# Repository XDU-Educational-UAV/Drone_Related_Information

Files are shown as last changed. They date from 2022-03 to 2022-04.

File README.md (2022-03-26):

微型四轴飞行器外形:

         HEAD
	M4  ↑  M1
	   \     /
	    \   /
	     \ /
	     / \
	    /   \
	   /     \
	M3     M2
	
硬件资源:

1. MCU:STM32G030K8T6 (FLASH:512K, RAM:128K, 系统运行时钟频率:96MHz)
2. 6轴MPU6050连接在IIC1上(IMU_SCL:PB8, IMU_SDA:PB7, 通信方式:模拟IIC)
3. 蓝牙无线通信NFR51822连接在UART1上(RXD:PA3, TXD:PA2, NRF_FLOW_CTRL:PA4)
4. MOTOR1连接在TIM4_CH2上(PB6)
5. MOTOR2连接在TIM4_CH1上(PB3)
6. MOTOR3连接在TIM2_CH3上(PA9/PA11)
7. MOTOR4连接在TIM2_CH1上(PB8)
8. MOTOR1对应的绿色LED，连接在PB5上，高电平有效
9. MOTOR2对应的绿色LED，连接在PB4上，高电平有效
10. MOTOR3对应的绿色LED，连接在PC8上，高电平有效
11. MOTOR4对应的绿色LED，连接在PB9上，高电平有效

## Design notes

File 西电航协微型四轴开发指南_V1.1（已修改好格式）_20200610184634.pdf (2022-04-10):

XDU Aero Association | 西电航协

51 /
58

# 西电航协微型四轴开发指南

主编&项目策划： | 西安电子科技大学 电子工程学院 吕瑞涛
硬件设计： | 西安电子科技大学 电子工程学院 王晗宇
机械设计： | 西安电子科技大学 空间科学与技术学院 程天宇
软件设计： | 西安电子科技大学 电子工程学院 吕瑞涛 李妍榕

### User Manual

用户手册

目 录

目录

# 1. 四轴飞行器的基本组成

四轴飞行器主要是由电机、电调、电池、浆叶、机架、遥控器、飞控组成。下面我们 分别以我们微型四轴及市场上常见的 DIY 大四轴来介绍这些部件。

# 1.1 电机

电机分为有刷电机和无刷电机两类，分别如图 1.1.1 和图 1.1.2 所示。

图 1.1.1 空心杯电机 | 图 1.1.2 无刷电机

有刷电机体积小价格便宜而且控制简单，比较适用于做微型四轴。我们设计的微型四 轴就是采用了图 1.1.1 空心杯有刷电机，型号为 716。 无刷电机体积稍大，载重能力强，比较适用于 DIY 大四轴。无刷电机控制需要搭配专 门的无刷电机电调模块。如图 1.1.2 无刷电机，2212 1200KV，22 表示电机的外转子直径为 22mm；12 表示转子的高度为 12mm；1200KV 表示电压每增加 1V 电机的转速增加

## 1200r/min。

# 1.2 MOS 管和电调

微型四轴和大四轴一般分别使用 MOS 管和电调驱动电机，MOS 管和电调分别如图

## 1.2.1 和 1.2.2 所示：

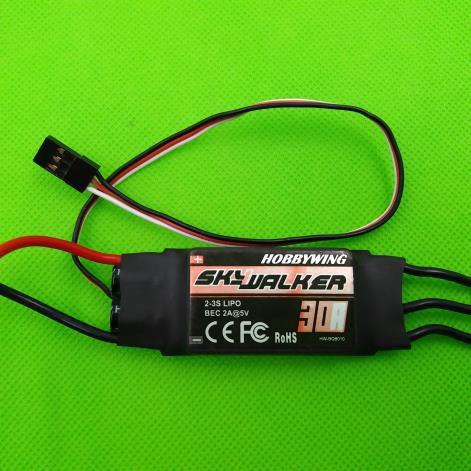
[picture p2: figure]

图 1.2.1 MOS 管 | 图 1.2.2 无刷电机电调模块

电调即为电子调速器，控制电机转动、停止及转速。
有刷电机电调通常只需要一个 MOS 管，飞控输出 PWM 即可控制电机。我们设计的 微型四轴采用如图 1.2.1 所示 SOT-23 封装的 MOS 管，型号为：SI2302。

无刷电机电调模块如图 1.2.2 所示。无刷电机电调模块内部通常由一个 MCU 和三相 桥电路组成，MCU 通过控制三相桥来实现无刷电机换相。同样，无刷电机电调模块也只需 飞控输出 PWM 即可控制电机。

## 1.3 航模电池

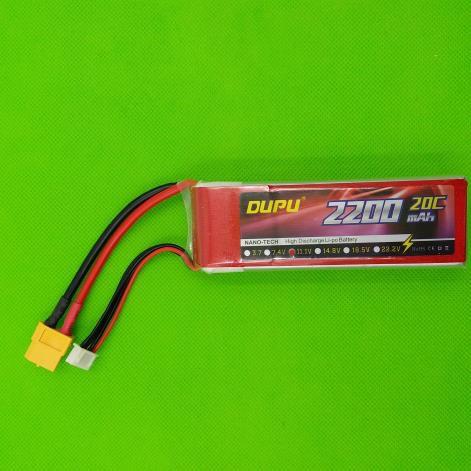
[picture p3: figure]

微型四轴选用的锂电池如图 1.3.1 所示，参数为 250mAh 20C 1S。DIY 大四轴常用的 锂电池如 1.3.2 所示。

图 1.3.1 250mAh 20C 1S 锂电池 | 图 1.3.2 2200mAh 20C 3S 锂电池
下面我们对这些参数做一下解释。
电池容量 mAh：锂电池的容量，如 2000mAh 的电池，以 2000mA 放电，可持续放电 1 小时；以 1000mA 放电，可持续放电 2 小时。
电池节数：电池 2S、3S、4S 代表锂电池节数。锂电池 1 节的标准电压为 3.7V，3S 代表有 3 节 3.7V 的电池在里面，电压为 11.1V。
电池放电倍率 C：四轴一般使用的动力锂电池，也是放电倍率 C 较大。普通锂电池放 电倍率通常为 1C 或者 0.5C，动力电池则为十几二十 C。如标称 250mAh 20C 的电池，它 的放电电流为 250ma×20，即为 5A 放电电流。

# 1.4 正反桨

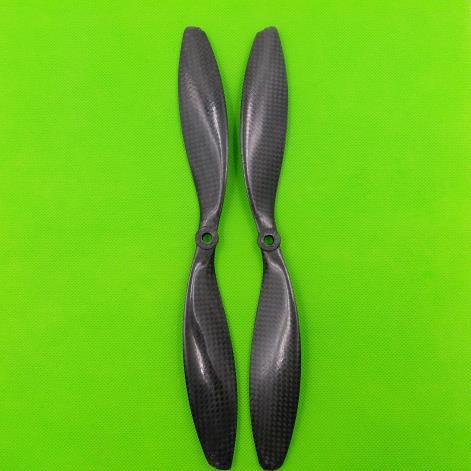
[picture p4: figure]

微型四轴选用如图 1.4.1 所示，直径为 46mm 的浆叶，带 A 字的浆为正浆。图 1.4.2 1038 正反浆叶为 DIY 大四轴所用的浆叶，1038 表示直径 10 英寸，螺距 3.8 英寸。

图 1.4.1 46mm 正反浆叶 | 图 1.4.2 1038 正反浆叶

四轴飞行器为什么需要正反浆叶？
答：浆叶旋转时会产生自旋力导致四轴自旋，为了抵消自旋力相隔电机的浆叶旋转方向要 不一样，但是浆的风都是要往下吹，这就出现了正反浆的说法。通常顺时针转的叫正浆，逆 时针转的是反浆。

## 1.5 四轴机架

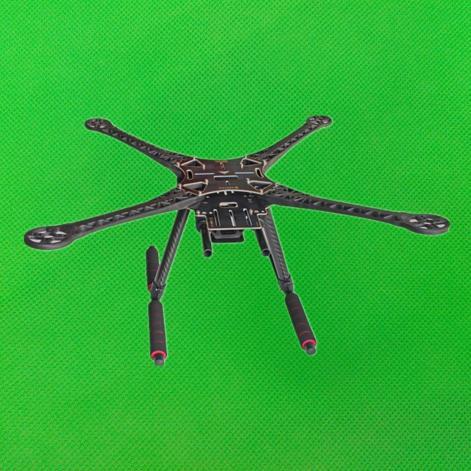
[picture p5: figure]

机架一般采用质轻、硬度好的材料，大四轴常采用碳纤维材质或尼龙材质作为机架。 小四轴使用硬塑料材质或 PCB 都可以。微型四轴直接采用轻木板作为支架，支架集成控制 电路一体不仅小巧美观而且功能齐全，如图 1.5.1 所示。DIY 大四轴常用的碳纤维支架， 如图 1.5.2 所示。

图 1.5.1 PCB 机架 | 图 1.5.2 碳纤维支架

## 1.6 四轴遥控器

微型四轴遥控器采用蓝牙控制，简便快捷。如图 1.6.2 所示的商业遥控器采用的是日 本手方式。商业遥控也有美国手的，购买时根据自己的操作习惯区分购买。

图 1.6.2 商业遥控器
遥控器用于发送各种控制指令，常用通信频段为 2.4G。四轴飞行器的控制至少需要 4 个通道，功能越多需要的通道数越多。遥控器按操作习惯可分为美国手和日本手两种。 什么是遥控器通道？

答：通道就是可以遥控器控制的动作路数。四轴在控制过程中需要控制的动作路数有： 上下、左右、前后、旋转。所以最低得 4 通道遥控器。

什么是美国手、日本手？
答：油门摇杆在左边、方向摇杆在右边是美国手；相反，油门摇杆在右边、方向摇杆 在左边是日本手。

## 1.7 四轴飞控

微型四轴飞控如图 1.7.1 所示。国外 APM 飞控如图 1.7.2 所示，

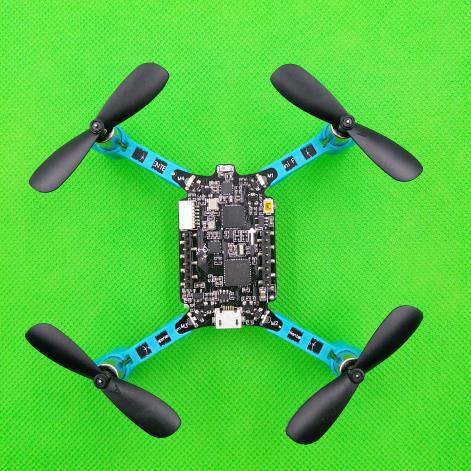
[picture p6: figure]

图 1.7.1 微型四轴飞控 | 图 1.7.2 APM 飞控和遥控器接收机
飞控是四轴飞行器的核心部件，主要由 MCU、陀螺仪、加速度计、磁力计、气压 计、无线接收模块等组成。飞控采集各路传感器数据，经过姿态解算求出姿态，然后对比 遥控器发过来的控制命令数据，再经过 PID 计算出控制量，最后将控制量转换成 PWM 信 号，分别控制各个电机。
遥控器接收机是接收遥控信号的，它与遥控器是配套的。

# 2. 四轴飞行器的基本工作原理

四轴飞行器基本原理是通过飞控控制四个电机旋转带动浆叶产生升力，分别控制每一个 电机和浆叶产生不同的升力从而控制飞行器的姿态和位置。四轴在空中可以实现八种运动， 分别为垂直上升、垂直下降、向前运动、向后运动、向左运动、向后运动、顺时针改变航 向、逆时针改变航向。下面分别介绍实现的这些动作的原理。

## 2.1 垂直上升和垂直下降

当四轴飞行在空中自稳后，M1、M2、M3、M4 四个电机同时转速增大或同时转速减小， 即可发生垂直上升运动或垂直下降运动，分别如图 2.1.1 和图 2.1.2 所示：。

图 2.1.1 垂直上升 | 图 2.1.2 垂直下降

## 2.2 向前运动和向后运动

如图 2.2.1 所示，当四轴飞行在空中自稳后，M2、M3 转速增大 M1、M4 转速不变或减 小即可实现向前运动。相反，如图 2.2.2 所示，M2、M3 转速减小或不变 M1、M4 转速增加 即可实现向后运动。

图 2.2.1 向前运动 | 图 2..2.2 向后运动

## 2.3 向左运动和向后运动

如图 2.3.1 所示，当四轴飞行在空中自稳后，M1、M2 转速增大 M3、M4 转速不变或减 小即可实现向左运动。相反，如图 2.3.2 所示，M1、M2 转速减小或不变 M3、M4 转速增加 即可实现向右运动。

图 2.3.1 向左运动 | 图 2.3.2 向右运动

## 2.4 顺时针改变航向和逆时针改变航向

如图 2.4.1 所示，当四轴飞行在空中自稳后，M1、M3 转速增大 M2、M4 转速不变或减 小即可实现顺时针改变航向。相反，如图 2.4.2 所示，M1、M3 转速减小或不变 M2、M4 转 速增加即可实现逆时针改变航向。

图 2.4.1 顺时针改变航向 | 图 2.4.2 逆时针改变航向

# 3. 航模常见术语

# 3.1 X 模式和+模式

从结构形式上四轴飞行器可分为十字模式和 X 模式。十字模式如下图 3.1.1 所示，X 模式如下图 3.1.2 所示。对于姿态测量和控制来说，两种结构差别不大。如果考虑安装航 拍摄像机，为了视线不被挡住，通常采用 X 模式。

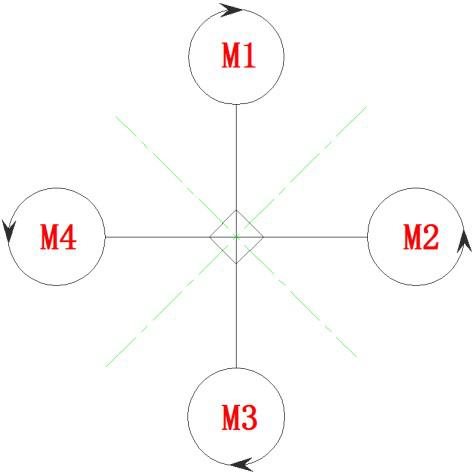
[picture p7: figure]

图 3.1.1 十字模式 | 图 3.1.2 X 模式

# 3.2 姿态角 pitch/roll/yaw

图 3.2.1 地面坐标系 | 图 3.2.2 机体坐标系
地面坐标系，如图 3.2.1 所示：
- 在地面上选一点 Og；
- 使 Xg 轴在水平面内并指向某一方向；
- Zg 轴垂直于地面并指向地心；
- Yg 轴在水平面内垂直于 Xg 轴，其指向按右手定则确定；机体坐标系，如图 3.2.2 所 示：
- 原点 O 取在飞机质心处，坐标系与飞机固连；
- X 轴在飞机对称平面内并平行于飞机的设计轴线指向机头；
- Y 轴垂直于飞机对称平面指向机身右方；
- Z 轴在飞机对称平面内，与 X 轴垂直并指向机身下方；

姿态角（pitch、roll、yaw）是飞行器的机体坐标系与地面坐标系的夹角，也叫做欧拉 角（Euler Angle）。飞行器在空中任何一种姿态都可以通过姿态角旋转后得到。姿态角的 旋转关系图如下图 3.2.3 所示。

图 3.2.3 姿态角旋转关系图
俯仰角（pitch）：机体坐标系 X 轴与水平面的夹角，围绕 X 轴旋转。当 X 轴的正半 轴位于过坐标原点的水平面之上（抬头）时，俯仰角为正，否则为负。 偏航角（yaw）：机体坐标系 X 轴在水平面上投影与地面坐标系 Xg 轴之间的夹角， 围绕 Y 轴旋转。机头右偏航为正，反之为负。
滚转角（roll）：机体坐标系 Z 轴与通过机体 Z 轴的铅垂面间的夹角，围绕 Z 轴旋转。

机体向右滚为正，反之为负。

## 3.3 有头模式和无头模式

有头模式：飞行器运动的前后左右以自身的坐标系为参考坐标系。当飞行器旋转（航 向角改变）后，前进方向始终是机头的方向。
无头模式：飞行器运动的前后左右以地面坐标系为参考坐标系。当飞行器旋转（航向 角改变）后，前进方向始终是初始设定的前进方向。

# 4. 微型四轴硬件资源

## 4.1 系统框架

微型四轴系统框架如图 4.1.1 所示：

图 4.1.1 系统框架

可以看到，微型四轴采用 STM32G030K8T6 MCU 控制，JDY-32 蓝牙模块主要负责无线 通信，Cortex-M0 内核 MCU 主要负责传感器读取，数据融合，PID 控制和电机控制等。而 这 2 个模块 之间的通信方式为 UART。电路原理详细分析请接着往下看。

# 4.2 主控 MCU 接口

## 主控 MCU STM32G030K8T6 电路图如图 4.2.1 所示：

## 图 4.2.1 主控 MCU

## 主控 MCU 采用 STM32G030K8T6, 该 32-bit Cortex-M0 内核芯片比较强大，集成 FPU

和 DSP 指令，并具有 64KB FLASH、3 个 16 位定时器、2 个 32 位定时器、2 个 DMA 控制

## 器、5 个 SPI（全双工 I2S）、3 个 IIC、2 个串口、1 个 USB（支持 HOST/SLAVE）、16

通道 12 位 ADC、1 个 RTC（带日历功能）、1 个 SDIO 接口、以及 36 个通用 IO 口等。 主控 MCU 为四轴飞行器的大脑，对飞行器稳定飞行起着至关重要的作用。它同时承 担着多种责任，包括：传感器数据读取、数据融合、PID 控制、电机控制、无线通信等。 主控 MCU 通过 UART2 串口连接了一个蓝牙模块，此模块可以用作微型四轴与上位机 通信，也可用于安卓设备控制该四轴。

## 4.3 传感器接口

微型四轴板载一颗六轴传感器 MPU6050 ，电路图如图 4.3.1 所示：

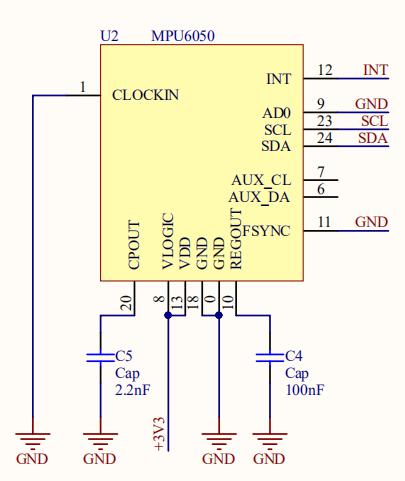
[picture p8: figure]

## 图 4.3.1 MPU6050 六轴传感器

六轴传感器芯片为 MPU6050，该芯片内部集成了 3 轴加速度传感器、3 轴陀螺仪传感

## 器。并且自带 DMP(Digital Motion Processor)，支持 MPL。此传感器用于测量四轴的姿态数

据。
MPU6050 支持 SPI 和 IIC 通信。为方便开发，这 2 颗传感器我们都使用 IIC 通信，

## MPU6050 挂接在 MCU 的硬件 IIC1 接口（IMU_SCL:PB8, IMU_SDA:PB7）上，而且我们

使用模拟 IIC 的通信方式，因为模拟 IIC 的通信方式已经能满足我们要求。我们可以看到

## MPU6050 的 IIC 地址为 0xD2。

## 4.4 电机接口

微型四轴板载四个便携式插拔电机接口，电路图如图 4.4.1 所示：

图 4.4.1 电机接口
微型四轴采用微型高速 716 空心杯电机，电机转速高达 45000r/min，能够为飞行器提供 充沛的动力。电机采用 NMOS 管 SI2302，3V 门级驱动电压下，导通电阻只有几十毫欧，驱 动电流高达 3A，轻松驱动 716 空心杯电机，从而带动飞行器飞行。

## 4.5 无线通信和 PA 接口

微型四轴板载一颗蓝牙无线通信芯片 JDY-32，电路图如图 4.5.1 所示：

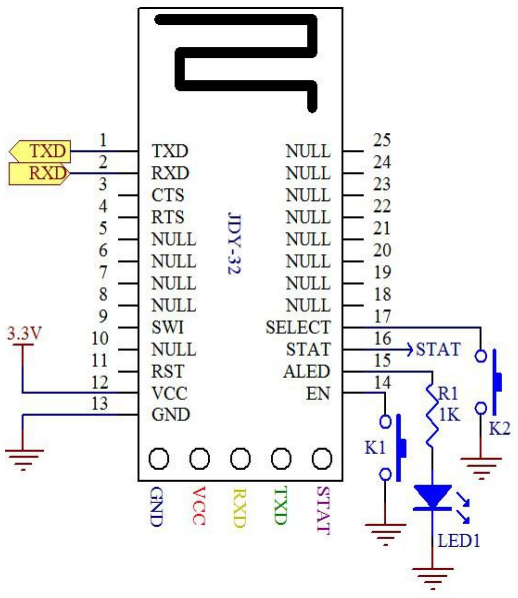
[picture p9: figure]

图 4.5.1 蓝牙无线通信芯片 JDY-32
JDY-32 双模蓝牙基于蓝牙 3.0 SPP + 蓝牙 4.2 BLE 设计，这样可以支持 Windows、 Linux、 ios、android 数据透传，工作频段 2.4GHZ，调制方式 GFSK，最大发射功率 5db，最 大发射距离 40 米，支持用户通过 AT 命令修改设备名、波特率等指令，方便快捷使用灵活。 JDY-32 支持经典蓝牙与 BLE 协议、可以与支持蓝牙的电脑（台式、笔记本）、手机 （android、IOS）通信。

该蓝牙模块通信接口为 UART，工作频段为 2.4GHz，工作电压为 1.8V-3.6V（建议 3.3V），采用 Bluetooth 4.2 BLE/Bluetooth 3.0 SPP 的蓝牙版本。它和主控 MCU 的通信

## 是通过 UART2（NRF_RX:PA2, NRF_TX:PA3, NRF_FLOW_CTRL:PA0）。该模块内置 PCB

天线，传输距离 <= 40 m，发射功率最大为 5db。

该模块的串口指令集如下表所示：

### 注：JDY-32 模块串口发送 AT 指令务必加上\r\n

序列 | 指令 | 功能 | 默认
1 | AT+VERSION | 版本号 | JDY-32-V1.0
2 | AT+RST | 软复位
3 | AT+DISC | AT 指令断开连接
4 | AT+MAC | 查询 BLE 的 MAC 地址
5 | AT+MACS | 查询 SPP 的 MAC 地址
6 | AT+BAUD | 波特率 | 9600
7 | AT+NAME | BLE 广播名设置与查询 | JDY-32-LE
8 | AT+NAMES | SPP 广播名设置与查询 | JDY-32-SPP
9 | AT+TYPE | SPP 密码连接类型 | 2
10 | AT+PIN | SPP 连接密码 | 1234
11 | AT+DEFAULT | 恢复出厂设置

## 4.6 电源接口

微型四轴板载的电源接口部分，其电路图如图 4.6.1 所示：

图 4.6.1 电源接口

ME6206A 是高纹波抑制率、低功耗、低压差，具有过流和短路保护的 CMOS 降压型线性稳 压器（LDO）。这些器件具有很低的静态偏置电流，它们能在输入、输出电压差极小的情况 下提供 300mA 的输出电流，并且仍能保持良好的调整率。该器件输入电压高达 6.0V，输出

1.5V - 5.0V。因为是线性稳压器，所以输出纹波很小，同时低压差的功能就可以保证输入电 压在很低的条件下输出电压也非常稳定。

# 4.7 LED 接口

微型四轴板载 4 颗高亮的绿色 LED ，其电路图如图 4.7.1 所示：

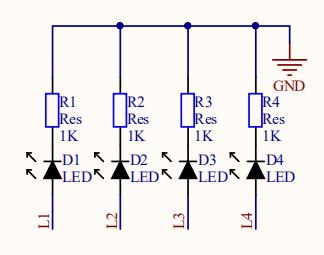
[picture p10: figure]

## 图 4.7.1 LED 接口

## 4.8 下载接口

微型四轴板载 SWD 仿真及下载接口，电路图如图 4.9.1 所示： 图 4.9.1 SWD 仿真下载接口

微型四轴为客户预留了代码下载和调试接口，方便客户二次开发。该接口支持 STM32 的代码下载和调试。

# 5. STM32 基础知识

## 5.1 STM32 时钟树原理

我们可以把 MCU 的运行比作人体的运行一样，人最重要的是什么？是心跳！ 心脏的 周期性收缩将血液泵向身体各处。心脏对于人体好比时钟对于 MCU，微控制器（MCU） 的运行要靠周期性的时钟脉冲来驱动，而这个脉冲的始源往往是由外部晶体振荡器提供 时钟输入，最终转换为多个外部设备的周期性运作。这种时钟“能量”的传递路径犹如大树 的养分由主干流向个分支，因此称为时钟树。

在 STM32 中每个外设都有其单独的时钟，在使用某个外设之前必须打开该外设的时 钟 ，为什么要这么麻烦来设置每一个外设的时钟而不是将所有外设的时钟统一打开？因 为 STM32 的外设繁多，外设的运作所需要的最佳时钟各不相同，如果所有时钟同时运行 会给 MCU 带来极大的负载，所以 STM32 采取自助餐式的时钟管理方式——随用随开。

各类时钟简括：

1.HSE 时钟（高速外部时钟）：来源为外部无源晶振，通常速度 8M。由 RCC_CR 时钟 控制寄存器中的 16:HSEON 控制。

2.HSI 时钟（高速内部时钟）：来源为芯片内部，大小为 8M，当 HSE 故障时，系统时 钟会自动切换到 HSI，知道 HSE 启动成功，相当于 HSE 的替补。由 RCC_CR 时钟控制寄存

## 器的位 0:HSION 控制。

3.PLLCLK（锁相环时钟）：来源为 HSI/2、HSE 经过倍频所得。由 CFGR(时钟配置寄存

## 器)中 PLLXTPRE、PLLMUL 控制。 4.SYSCLK（系统时钟）：来源为 HSI、HSE、PLLCLK，最高速度为 72M。由 CFGR 中的

SW 控制。

5.HCLK（AHB 高速总线时钟）：来源由系统时钟分频得到，速度最高为 72M。由

## CFGR 中的 HPRE 控制。

6.PCLK1（APB1 低总线时钟）：来源为 HCLK 分频得到，速度最高为 36M ，为 APB1 总线上的外设提供时钟。由 RCC_CFGR 时钟配置寄存器的 PPRE1 位控制。

7.PCLK2（APB2 高总线时钟）：来源为 HCLK 分频得到，速度最高为 72M，为 APB2 总 线上的外设提供时钟。由 RCC_CFGR 时钟配置寄存器的 PPRE2 位控制。

## 8.RTC 时钟：来源为 HSE_RTC（HSE 分频得到）、LSE、LSI，为芯片内部的 RTC 外设提

供时钟。由 RCC 备份域控制寄存器 RCC_BDCR 中 RTCSEL 控制。

## 5.2 STM32 GPIO 原理

STM32G0 每组通用 I/O 端口包括 4 个 32 位配置寄存器（MODER、OTYPER、OSPEEDR 和 PUPDR）、2 个 32 位数据寄存器（IDR 和 ODR）、1 个 32 位置位/复位寄存器(BSRR)、 1 个 32 位锁定寄存器(LCKR) 和 2 个 32 位复用功能选择寄存器（AFRH 和 AFRL）等。 GPIO 可以配置成以下 8 种工作模式：

浮空输入：此端口在默认情况下什么都不接，呈高阻态，这种设置在数据传输时用的 比较多。
上拉输入：上拉输入模式与浮空输入模式相比，仅仅是在数据通道上部，接入了一个 上拉电阻，这个上拉电阻的阻值介于 30K~50K 欧姆，CPU 可以随时在输入数据寄存器的另 一端，读出 I/O 端口的电平状态。这种模式的好处在于我们什么都不输入时，由于内部上 拉电阻的原因，处理器会觉得我们输入了高电平，这就避免了不确定的输入。该端口在默 认情况下输入为高电平。
下拉输入：下拉输入模式与浮空输入模式相比，仅仅是在数据通道上部，接入了一个 下拉电阻。与上拉输入模式类似，这种模式的好处在于外部没有输入时，由于内部下拉电 阻的原因，我们的处理器会觉得我们输入了低电平。
模拟功能：STM32 的模拟输入通道的配置很简单，信号从 I/O 端口直接进入 ADC 模 块。此时，所有的上拉、下拉电阻和施密特触发器，均处于断开状态，因此输入数据寄存 器将不能反映端口上的电平状态，也就是说，模拟输入配置下，信号不经过输入数据寄存 器，CPU 不能在输入数据寄存器上读到有效的数据。该输入模式，使我们可以获得外部的 模拟信号。
开漏输出：开漏输出不可以直接输出高电平，开漏输出的输出端相当于三极管的集电 极，要得到高电平状态需要上拉电阻才行。
推挽输出：推挽输出可以输出高、低电平，连接数字器件；推挽结构一般是指两个三 极管分别受两个互补信号的控制，总是在一个三极管导通的时候另一个截止。高低电平由 IC 的电源决定。
开漏复用输出：GPIO 的基本功能是普通的 I/O，而 STM32 有自己的各个功能模块，这 些内置外设的外部引脚是与标准 GPIO 复用的，当作为这些模块的功能引脚时就叫复用。开 漏复用输出功能模式与开漏输出模式相比，不同的是输出控制电路的输入，是和片上外设 的输出信号相连即与复用功能的输出端相连，此时，输出数据寄存器在输出通道被断开。 推挽复用输出：推挽复用输出功能模式与推挽输出模式相比，不同的是输出控制电路 的输入，是和片上外设的输出信号相连，即与复用功能的输出端相连，而输出数据寄存器 在输出通道被断开。

## 5.3 STM32 NVIC 原理

NVIC 的全称是 Nested vectored interrupt controller，即嵌套向量中断控制器。

通常，在接收到来自外围硬件（相对于中央处理器和内存）的异步信号，或来自软件的 同步信号之后，处理器将会进行相应的硬件／软件处理。发出这样的信号称为进行中断请求 （interrupt request，IRQ）。硬件中断导致处理器通过一个运行信息切换（context switch）来保存执行状态（以程序计数器和程序状态字等寄存器信息为主）；软件中断则通 常作为 CPU 指令集中的一个指令，以可编程的方式直接指示这种运行信息切换，并将处理导 向一段中断处理代码。中断在计算机多任务处理，尤其是即时系统中尤为有用。
对于 M3 和 M4 内核的 MCU，每个中断的优先级都是用寄存器中的 8 位来设置的。8 位的话 就可以设置 2^8 =256 级中断，实际中用不了这么多，所以芯片厂商根据自己生产的芯片做出 了调整。比如 ST 的 STM32F1xx 和 F4xx 只使用了这个 8 位中的高四位[7:4]，低四位取零，这 样 2^4=16，只能表示 16 级中断嵌套。
对于这个 NVIC，有个重要的知识点就是优先级分组，抢占优先级和子优先级，下面就以 STM32 为例进行介绍，STM32G030 是只使用了这个 8 位寄存器的高四位[7:4]。

## 图 5.3 NVIC 优先级

具有高抢占式优先级的中断可以在具有低抢占式优先级的中断服务程序执行过程中被 响应，即中断嵌套，或者说高抢占式优先级的中断可以抢占低抢占式优先级的中断的执 行。在抢占式优先级相同的情况下，有几个子优先级不同的中断同时到来，那么高子优 先级的中断优先被响应。

在抢占式优先级相同的情况下，如果有低子优先级中断正在执行，高子优先级的中断 要等待已被响应的低子优先级中断执行结束后才能得到响应，即子优先级不支持中断嵌 套。Reset、NMI、Hard Fault 优先级为负数，高于普通中断优先级，且优先级不可配 置。

## 5.4 STM32 EXTI 原理

EXTI（External interrupt/event controller）—外部中断/事件控制器，管理了控制 器的 20 个中断/事件线。每个中断/事件线都对应有一个边沿检测器，可以实现输入信号的上 升沿检测和下降沿的检测。EXTI 可以实现对每个中断/事件线进行单独配置，可以单独配置 为中断或者事件，以及触发事件的属性。

外部中断的触发方式有：电平触发和跳沿触发。
边沿触发和电平触发基本就是触发器和锁存器的区别。触发器是边沿触发，只有当时钟 上升（或下降）的一瞬间，触发器会读取并锁存输入信号。输出信号仅在时钟信号上升（或 下降）的一瞬间会发生变化。锁存器是电平触发，只要使能（enable）信号处于高电平（或 低电平），输出就会随着输入信号变化，直到使能信号变为低电平（或高电平）时，输出才 会锁存，不再随输入变化。
STM32 上每个 IO 都可以作为外部中断输入，其中断控制器支持 22 个外部中断/时间请 求。

EXTI 线 0~15：对应外部 IO 口的输入中断。
EXTI 线 16：连接到 PVD 输出。
EXTI 线 17：连接到 RTC 闹钟事件。
EXTI 线 18：连接到 USB OTG FS 唤醒事件。

EXTI 线 19：连接到以太网唤醒事件。
EXTI 线 20：连接到 USB OTG HS(在 FS 中配置)唤醒事件。
EXTI 线 21：连接到 RTC 入侵和时间戳事件。
EXTI 线 22：连接到 RTC 唤醒事件。
每个外部中断线可以独立的配置触发方式（上升沿，下降沿或者双边沿触发），触发/屏 蔽，专用的状态位。但是值得注意的是：外部 IO 口有 16 条中断线，但并不是能设置 16 个外 部中断，一组 IO 口对应一根中断线，每个 IO 口都可以使用这跟中断线，但是在同一时刻， 只能响应一个端口的事件触发，不能同时响应所有 GPIO 端口的事件，也就是分时复用。 IO 口外部中断在中断向量表中只分配了 7 个中断向量，也就是只能使用 7 个中断服务函 数。
中断线 0 ~ 4 各对应一个中断函数
中断线 5 ~ 9 共用中断函数 EXTI9_5_IRQHandler
中断线 10 ~ 15 共用中断函数 EXTI15_10_IRQHandler

## 5.5 STM32 ADC 和 DMA 原理

### 5.5.1 STM32 ADC 原理

## ADC（Analog-to-Digital Converter，模/ 数转换器）。也就是将模拟信号转换为数字信

号进行处理，在存储或传输时，模数转换器几乎必不可少。

STM32 ADC 特点

12 位逐次逼近型的模拟数字转换器。
最多带 3 个 ADC 控制器
最多支持 18 个通道，可最多测量 16 个外部和 2 个内部信号源。 支持单次和连续转换模式
转换结束，注入转换结束，和发生模拟看门狗事件时产生中断。 通道 0 到通道 n 的自动扫描模式
自动校准
采样间隔可以按通道编程
规则通道和注入通道均有外部触发选项
转换结果支持左对齐或右对齐方式存储在 16 位数据寄存器
ADC 转换时间：最大转换速率 1us。（最大转换速度为 1MHz，在 ADCCLK=14M ， 采 样 周期为 1.5 个 ADC 时钟下得到。）
ADC 供电要求：2.4V-3.6V
ADC 输入范围：VREF- ≤ | VIN | ≤ | VREF+

### 5.5.2 STM32 DMA 原理

DMA(Direct Memory Access：直接内存存取)是一种可以大大减轻 CPU 工作量的数据转移 方式。

CPU 有转移数据、计算、控制程序转移等很多功能，但其实转移数据（尤其是转移大量数 据）是可以不需要 CPU 参与。比如希望外设 A 的数据拷贝到外设 B，只要给两种外设提供一条 数据通路，再加上一些控制转移的部件就可以完成数据的拷贝。

DMA 就是基于以上设想设计的，它的作用就是解决大量数据转移过度消耗 CPU 资源的问 题。有了 DMA 使 CPU 更专注于更加实用的操作--计算、控制等。

DMA 的作用就是实现数据的直接传输，而去掉了传统数据传输需要 CPU 寄存器参与的环 节，主要涉及四种情况的数据传输（外设到内存、内存到外设、内存到内存、外设到外 设），但本质上是一样的，都是从内存的某一区域传输到内存的另一区域（外设的数据寄存 器本质上就是内存的一个存储单元）。

### 5.5.3 DMA 在 AD 转换中的作用

ADC 采集到的数据是不能直接用的，单次采集会出现不准确的数据，所以要多次采样才能 减小系统误差。也可以说，单次 ADC 采集无意义。多次采样造成了数据传输量大，因此我们 需要独立于 Cortex 内核的 DMA 模块，实现通信“桥梁”的作用，将外设映射的寄存器“连 接”起来，这样我们就可以高速访问各个寄存器，其传输不受 CPU 的支配。

## 5.6 STM32 PWM 原理

## 脉冲宽度调制(PWM)，是英文“Pulse Width Modulation”的缩写，简称脉宽调制，是利

用微处理器的数字输出来对模拟电路进行控制的一种非常有效的技术。简单一点，就是 对脉冲宽度的控制，PWM 原理如图 14.1.1 所示：

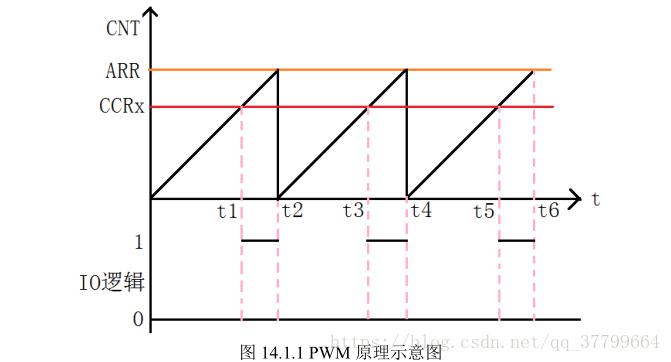
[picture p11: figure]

图 14.1.1 PWM 原理示意图

PWM 是一种对模拟信号电平进行数字编码的方法。通过高分辨率计数器的使用，方 波的占空比被调制用来对一个具体模拟信号的电平进行编码。PWM 信号仍然是数字的， 因为在给定的任何时刻，满幅值的直流供电要么完全有(ON)，要么完全无(OFF)。电压或 电流源是以一种通(ON)或断(OFF)的重复脉冲序列被加到模拟负载上去的。通的时候即是 直流供电被加到负载上的时候，断的时候即是供电被断开的时候。只要带宽足够，任何 模拟值都可以使用 PWM 进行编码。

STM32 的定时器除了 TIM6 和 7。其他的定时器都可以用来产生 PWM 输出。其中高 级定时器 TIM1 和 TIM8 可以同时产生多达 7 路的 PWM 输出。而通用定时器也能同时产 生多达 4 路的 PWM 输出，这样，STM32 最多可以同时产生 30 路 PWM 输出！

# 6. 四轴飞行器算法讲解

## 6.1 姿态解算简介

姿态解算指控制器读取自身传感器数据，实时计算四轴飞行器的姿态角，比如横滚角 （roll），俯仰角（pitch），偏航角（yaw）的信息，控制器根据这些信息即可计算 4 个电机 的输出量，使飞行器保持平衡稳定或者保持一定的倾斜角往设定方向飞行。姿态解算是飞行 器飞行的关键技术之一，解算速度和精度直接关系到飞行器飞行中的稳定性和可靠性。 姿态解算的方法有很多，比较典型的方法有扩展型卡尔曼滤波算法（EKF），互补滤波 算法等。扩展型卡尔曼滤波算法具有高精度的特点，但其计算量大，并要求建立精确的动力 学模型，因此并不是微型四轴飞行器的最佳选择；而互补滤波算法对系统的要求相对较低， 计算量也不大，在微型四轴飞行器的姿态解算中应用最广。

## 6.2 飞行器姿态表示方法

飞行器姿态有多种表示方式，常见的是四元数，欧拉角，矩阵和轴角。他们各自有其自 身的优点，在不同的领域使用不同的表示方式。在四轴飞行器中使用到了四元数和欧拉角。

## 6.2.1 欧拉角

用来确定定点转动刚体位置的 3 个一组独立角参量，由章动角 (http://baike.baidu.com/item/%E7%AB%A0%E5%8A%A8) θ、 (http://baike.baidu.com/item/%E6%97%8B%E8%BF%9B)旋进角（即进动 (http://baike.baidu.com/item/%E6%97%8B%E8%BF%9B) 角） ψ 和自转角 j 组成，为莱昂哈德·欧拉首先提出而得名。 对于在三维空间里的一个 (http://baike.baidu.com/item/%E4%B8%89%E7%BB%B4%E7%A9%BA%E9%97%B4)参考系，任何坐标系的取向，都可以用三个欧拉角来表现。 (http://baike.baidu.com/item/%E5%8F%82%E8%80%83%E7%B3%BB)参 考系又称为实验室参考系，是静止不动的。而坐标系则固定于刚体，随着刚体的 (http://baike.baidu.com/item/%E5%8F%82%E8%80%83%E7%B3%BB)旋转而旋 (http://baike.baidu.com/item/%E6%97%8B%E8%BD%AC) 转。
如图 5.2.1 所示：设定 xyz 轴为参考系的参考轴。称 (http://baike.baidu.com/item/%E5%8F%82%E8%80%83%E7%B3%BB) xy-平面与 XY-平面的相交为交点 线，用英文字母（N）代表。zxy 顺规的欧拉角可以静态地这样定义： α 是 x-轴与交点线的 夹角 (http://baike.baidu.com/item/%E5%A4%B9%E8%A7%92)，β (http://baike.baidu.com/item/%E5%A4%B9%E8%A7%92) 是 z-轴与 Z-轴的夹角，γ 是交点线与 X-轴的夹角。

很可惜地，对于夹角的顺序和标记，夹角的两个轴的指定，并没有任何常规。科学家对 (http://baike.baidu.com/item/%E5%A4%B9%E8%A7%92) 此从未达成共识。每当用到欧拉角时，我们必须明确的表示出夹角的顺序，指定其参考轴。 实际上，有许多方法可以设定两个坐标系的相对取向。欧拉角方法只是其中的一种。此 (http://baike.baidu.com/item/%E5%9D%90%E6%A0%87%E7%B3%BB) 外，不同的作者会用不同组合的欧拉角来描述，或用不同的名字表示同样的欧拉角。因此， 使用欧拉角前，必须先做好明确的定义。

## 图 5.2.1 欧拉角

本小节内容部分摘自百度百科 (http://baike.baidu.com/item/%E6%AC%A7%E6%8B%89%E8%A7%92)- (http://baike.baidu.com/item/%E6%AC%A7%E6%8B%89%E8%A7%92)欧拉角 (http://baike.baidu.com/item/%E6%AC%A7%E6%8B%89%E8%A7%92)

## 6.2.2 四元数

四元数（Quaternions）是由爱尔兰数学家哈密顿 (http://baike.baidu.com/item/%E5%93%88%E5%AF%86%E9%A1%BF/28890)(William (http://baike.baidu.com/item/%E5%93%88%E5%AF%86%E9%A1%BF/28890) Rowan Hamilton,1805- 1865）在 1843 年发明的数学概念。明确地说，四元数是复数的不可交换延伸。如把四元数

的集合考虑成多维实数空间的话，四元数就代表着一个四维空间，相对于复数为二维空间 (http://baike.baidu.com/item/%E4%BA%8C%E7%BB%B4%E7%A9%BA%E9%97%B4)。 (http://baike.baidu.com/item/%E4%BA%8C%E7%BB%B4%E7%A9%BA%E9%97%B4) 单位四元数与欧拉角、旋转矩阵是等价的，但又不同于欧拉角表示，四元数表示法没有 奇异点的问题，正因为这个优点，单位四元数在姿态估计的核心算法中非常常见。比起三维 旋转矩阵四元数更能方便的给出旋转的转轴和旋转角。
关于四元数的计算，四元数可以理解为一个实数和一个向量的组合，也可以理解为四 维的向量。这里用一个圈表示 q 是一个四元数（很可能不是规范的表示方式）。

四元数的长度（模）与普通向量相似。

下面是对四元数的单位化，单位化的四元数可以表示一个旋转。

四元数相乘，旋转的组合就靠它了。

旋转的“轴角表示”转“四元数表示”。这里创造一个运算 q(w,θ)，用于把绕单位向量 w 转 θ 角的旋转表示为四元数。

通过 q(w,θ)，引伸出一个更方便的运算 q(f,t)。有时需要把向量 f 的方向转到向量 t 的 方向，这个运算就是生成表示对应旋转的四元数的（后面会用到）。

然后是“四元数表示”转“矩阵表示”。再次创造运算，用 R(q)表示四元数 q 对应的矩阵 （后面用到）。

多个旋转的组合可以用四元数的乘法来实现。

“四元数表示”转“欧拉角表示”。用于显示。

本小节内容部分摘自百度百科 (http://baike.baidu.com/item/%E5%9B%9B%E5%85%83%E6%95%B0)- (http://baike.baidu.com/item/%E5%9B%9B%E5%85%83%E6%95%B0)四元数 (http://baike.baidu.com/item/%E5%9B%9B%E5%85%83%E6%95%B0)

## 6.3 软件姿态解算

我们先来看看如何用欧拉角描述一次平面旋转(坐标变换)，如图 5.3.1 所示：

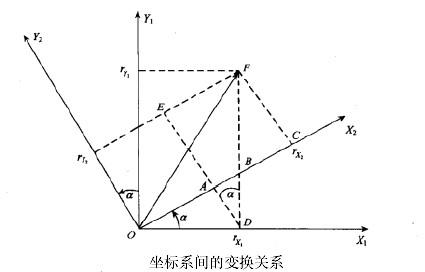
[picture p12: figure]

图 5.3.1 欧拉角平面旋转
设坐标系绕旋转 α 角后得到坐标系,在空间中有一个矢量在坐标系中的投影为,在内的 投影为由于旋转绕进行，所以 Z 坐标未变，即有：

转换成矩阵形式表示为：

整理一下：

上面仅仅是绕一根轴的旋转，如果三维空间中的欧拉角旋转要转三次:

上面得到了一个表示旋转的方向余弦矩阵，不过要想用欧拉角解算姿态，其实我们套用 欧拉角微分方程就行了：

上式中左侧是本次更新后的欧拉角,对应 roll、pitch、yaw。右侧是上个周期测算出来的 角度，三个角速度由直接安装在四轴飞行器的三轴陀螺仪在这个周期转动的角度，单位为弧 度，计算间隔时 T 陀螺角速度，比如 0.02 秒 0.01 弧度/秒=0.0002 弧度。间因此求解这个微

分方程就能解算出当前的欧拉角。
前面介绍了什么是欧拉角，而且欧拉角微分方程解算姿态关系简单明了，概念直观容 易理解，那么我们为什么不用欧拉角来表示旋转而要引入四元数呢？ 一方面是因为欧拉角微分方程中包含了大量的三角运算，这给实时解算带来了一定的困 难。而且当俯仰角为 90 度时方程式会出现神奇的“GimbalLock”。所以欧拉角方法只适用于 水平姿态变化不大的情况，而不适用于全姿态飞行器的姿态确定。 四元数法只求解四个未知量的线性微分方程组，计算量小，易于操作，是比较实用的工程 方法。
我们知道在平面(x,y)中的旋转可以用复数来表示，同样的三维中的旋转可以用单位四 元数来描述。我们来定义一个四元数：

我们可以把它写成,其中,。那么是矢量，表示三维空间中的旋转轴。w 是标量，表示旋 转角度。那么就是绕轴旋转 w 度，所以一个四元数可以表示一个完整的旋转。只有单位四 元数才可以表示旋转，至于为什么，因为这就是四元数表示旋转的约束条件。 而刚才用欧拉角描述的方向余弦矩阵用四元数描述则为：

更多参考资料请看：
秦永元《惯性导航》 袁信、郑锷的《捷联式惯性导航原理》，邓正隆的《惯性技术》

# 6.4 PID 控制理论

当今的闭环自动控制技术都是基于反馈的概念以减少不确定性。反馈理论的要素包括三 个部分：测量、比较和执行。测量关键的是被控变量的实际值，与期望值相比较，用这个偏 差来纠正系统的响应，执行调节控制。在工程实际中，应用最为广泛的调节器控制规律为比 例、积分、微分控制，简称 PID 控制，又称 PID 调节。
PID 控制器（比例-积分-微分控制器）是一个在工业控制应用中常见的反馈回路部件， 由比例单元 P、积分单元 I 和微分单元 D 组成。PID 控制的基础是比例控制；积分控制可 消除稳态误差，但可能增加超调；微分控制可加快大惯性系统响应速度以及减弱超调趋 势。这个理论和应用的关键是，做出正确的测量和比较后，如何才能更好地纠正系统。

## PID（比例（proportion）、积分（integral）、导数（derivative））控制器作为最早实用

化的控制器已有近百年历史，现在仍然是应用最广泛的工业控制器。PID 控制器简单易懂， 使用中不需精确的系统模型等先决条件，因而成为应用最为广泛的控制器，典型的单级 PID 控制器如图 5.4.1 所示：

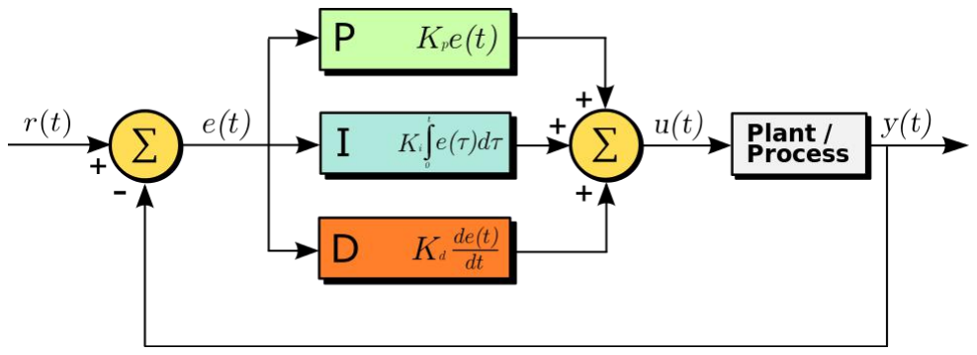
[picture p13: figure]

图 5.4.1 单级 PID 控制器结构框图比例（P）控制

比例控制是一种最简单的控制方式。其控制器的输出与输入误差信号成比例关系。当 仅有比例控制时系统输出存在稳态误差。比例项输出：

不同比例增益 Kp 下，受控变量的阶跃响应（Ki，Kd 维持稳定值）如图 5.4.2 所示：

图 5.4.2 不同比例增益下，系统对阶跃信号的响应积分（I）控制

在积分控制中，控制器的输出与输入误差信号的积分成正比关系。对于只有比例控制的 系统存在稳态误差，为了消除稳态误差，在控制器中必须引入“积分项”。积分项是误差对时 间的积分，随着时间的增加，积分项会增大。这样，即便误差很小，积分项也会随着时间的 增加而加大，它推动控制器的输出增大使稳态误差进一步减小，直到等于零。因此，比例积 分(PI)控制器，可以使系统在进入稳态后无稳态误差。 积分项输出：

不同积分增益 Ki 下，受控变量的阶跃响应（Kp，Kd 维持稳定值）如图 5.4.3 所示：

图 5.4.3 不同积分增益下，系统对阶跃信号的响应微分（D）控制

在微分控制中，控制器的输出与输入误差信号的微分成正比关系。微分调节就是偏差值 的变化率。使用微分调节能够实现系统的超前控制。如果输入偏差值线性变化，则在调节器 输出侧叠加一个恒定的调节量。大部分控制系统不需要调节微分时间。因为只有时间滞后的 系统才需要附加这个参数。微分项输出：

不同微分增益 Kd 下，受控变量的阶跃响应（Kp，Ki 维持稳定值）如图 5.4.4 所示：

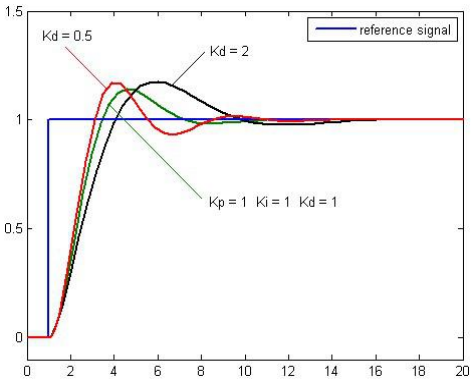
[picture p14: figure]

图 5.4.4 不同微分增益下，系统对阶跃信号的响应 综上可得到 PID 控制数学表达式：

更多内容请参考维基百科 (https://en.wikipedia.org/wiki/PID_controller)- (https://en.wikipedia.org/wiki/PID_controller)PID_controller (https://en.wikipedia.org/wiki/PID_controller)。 (https://en.wikipedia.org/wiki/PID_controller)

# 6.5 四轴常用的 2 种 PID

## 6.5.1 单级 PID

单级 PID 控制框图，如图 5.5.1 所示：

图 5.5.1 单级 PID 框图

期望角度就是遥控器控制飞行器的角度值，反馈当前角度就是传感器测得的飞行器角 度，这里的角度指的是 Roll/Pitch/Yaw 三个角度，而且在 PID 控制计算的时候，是相互独 立的。

## 6.5.2 串级 PID

角度单环 PID 控制算法仅仅考虑了飞行器的角度信息，如果想增加飞行器的稳定性(增 加阻尼)并提高它的控制品质，我们可以进一步的控制它的角速度，于是角度/角速度-串级 PID 控制算法应运而生。在这里，相信大多数朋友已经初步了解了角度单环 PID 的原理，

但是依旧无法理解串级 PID 究竟有什么不同。其实很简单：它就是两个 PID 控制算法，只 不过把他们串起来了(更精确的说是套起来)。那这么做有什么用？答案是，它增强了系统的 抗干扰性(也就是增强稳定性)，因为有两个控制器控制飞行器，它会比单个控制器控制更多 的变量，使得飞行器的适应能力更强。
串级 PID 控制框图，如图 5.5.2 所示：

## 图 5.5.2 串级 PID 框图

期望角度来自遥控数据，反馈角度来自传感器，二者的偏差作为外环角度环的输入，角 度环 PID 输出角速度的期望值；角速度期望值减去传感器反馈的角速度得到角速度偏差值， 这个值作为内环角速度环的输入，角速度环 PID 输出姿态控制量，控制量转换为 PWM 去控 制电机，从而控制四轴。

# 6.6 串级 PID 参数调试

内环 P：从小到大，拉动四轴越来越困难，越来越感觉到四轴在抵抗你的拉动；到比较 大的数值时，四轴自己会高频震动，肉眼可见，此时拉扯它，它会快速的振荡几下，过几秒 钟后稳定；继续增大，不用加人为干扰，自己发散翻机。特别注意：只有内环 P 的时候，四 轴会缓慢的往一个方向下掉，这属于正常现象。这就是系统角速度静差。
内环 I：前述 PID 原理可以看出，积分只是用来消除静差，因此积分项系数个人觉得没 必要弄的很大，因为这样做会降低系统稳定性。从小到大，四轴会定在一个位置不动，不再 往下掉；继续增加 I 的值，四轴会不稳定，拉扯一下会自己发散。特别注意：增加 I 的值， 四轴的定角度能力很强，拉动他比较困难，似乎像是在钉钉子一样，但是一旦有强干扰，它 就会发散。这是由于积分项太大，拉动一下积分速度快，给 的补偿非常大，因此很难拉动， 给人一种很稳定的错觉。
内环 D：这里的微分项 D 为标准的 PID 原理下的微分项，即本次误差-上次误差。在 角速度环中的微分就是角加速度，原本四轴的震动就比较强烈，引起陀螺的值变化较大， 此时做微分就更容易引入噪声。因此一般在这里可以适当做一些滑动滤波或者 IIR 滤波。 从小到大，飞机的性能没有多大改变，只是回中的时候更加平稳；继续增加 D 的值，可以 肉眼看到四轴在平衡位置高频震动(或者听到电机发出滋滋的声音)。前述已经说明 D 项属 于辅助性项，因此如果机架的震动较大，D 项可以忽略不加。
外环 P：当内环 PID 全部整定完成后，飞机已经可以稳定在某一位置而不动了。此时内 环 P，从小到大，可以明显看到飞机从倾斜位置慢慢回中，用手拉扯它然后放手，它会慢速 回中，达到平衡位置；继续增大 P 的值，用遥控器给不同的角度给定，可以看到飞机跟踪的 速度和响应越来越快；继续增加 P 的值，飞机变得十分敏感，机动性能越来越强，有发散的 趋势。
本节内容来自 CSDN 网友 Nemo 之家博客四轴 (http://blog.csdn.net/nemol1990/article/details/45131603) PID (http://blog.csdn.net/nemol1990/article/details/45131603) 讲解 (http://blog.csdn.net/nemol1990/article/details/45131603)

# 7. 微型四轴软件原理

# 7.1 STM32G030 程序解读

## 7.1.1 时钟树配置

本项目使用 STM32CubeMX 配置时钟树，使用 STM32CubeMX 的一个好处就是图形化配置， CubeMX 能自动检测时钟树配置的冲突并自动给出解决方案。在时钟配置方面，主要了解清楚 高级外设总线（APB1、APB2）控制哪些外设。

首先配置 RCC（复位和时钟控制），选择外部高速时钟，如下图所示：

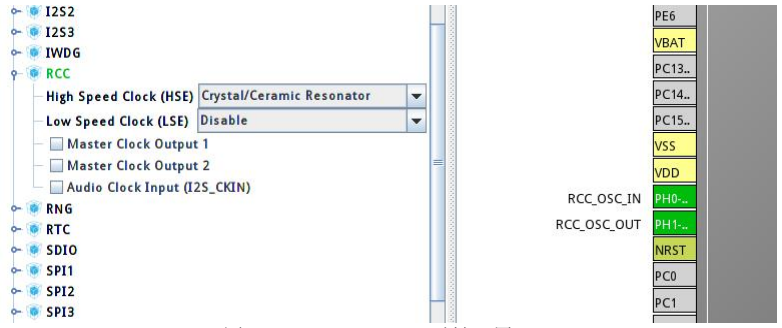
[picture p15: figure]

图 7.1.1 STM32CubeMX 时钟配置

通过查询 MCU 芯片手册，我们可以知道 TIM1 挂在 APB2 总线上，TIM2 挂在 APB1 总线 上。

进入时钟配置，STM32G030 开发板外部晶振是 8MHz 的，在 | Input | frequency | 输入
8，在 HCLK | 那里会提示最大频率 168MHz，输入 168，然后自动寻求配置，注意第一次配
置出来的还是内部时钟 HSI 的，要选择为 HSE，配置好后如下图。

图 7.1.2 STM32CubeMX 时钟树配置

设置定时器，以 TIM1 为例，APB2 时钟频率 168MHz=168,000,000Hz，选取预分频系数 (Prescaler)（16 位存储，预分频系数最大 65535）为 16799，则定时器的时钟频率为

168,000,000 / 16800 = 10000 Hz，频率为 1 万赫兹，选取计数周期(Counter Period，16 位存储）为 9999， 所以定时周期为 1s 。

牢记如下公式：

时钟周期=时钟频率/((时钟预分频系数+1)*(计数器自动重装载值+1))

在这里计数器自动重装载值(AutoReload Register)等于计数周期(Counter Period)， 因为计算机计数是从 0 开始的，因此这里我们需要给位于上式分母的两个值各加一。

同理 TIM2 也是同样计算，如果 APB 的时钟频率改变，一样安装上面的方法进行设置。

### 7.1.2 LED 指示灯配置

通过搜索框找到引脚的位置，这里我们分别设置 PB5，PB4，PC6，PA9 为 GPIO 输出模 式（即 GPIO_Output），并输入用户标签分别为 L1、L2、L3、L4（这里为了方便按照机臂 LED 顺序分别标注）。选中后，配置为输出模式后，该引脚变为绿色。

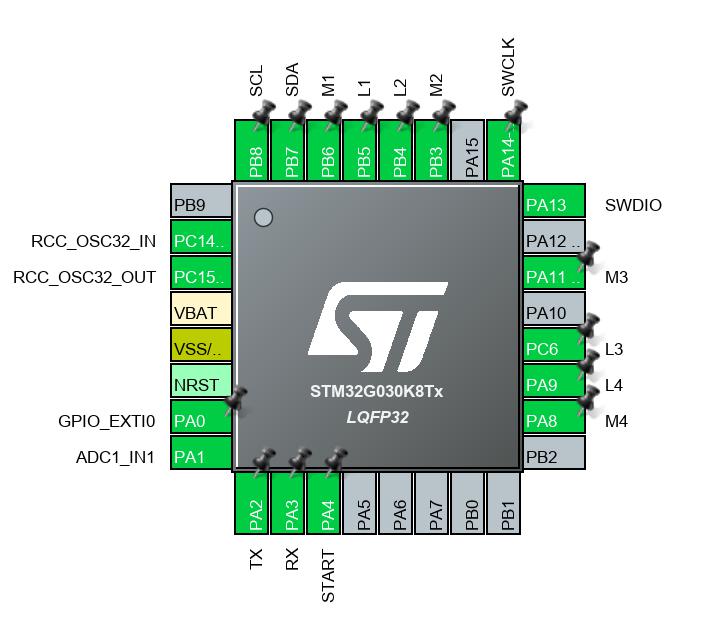
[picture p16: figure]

图 7.1.2 STM32CubeMX 引脚配置

接下来分别对两个 IO 进行详细配置，点击左边的 System Core，然后选择 GPIO,这时 候右边可以选中具体的引脚。我们分别配置 PB5、PB4、PC6、PA9 引脚的默认输出电平、 GPIO 工作模式、上下拉(这里配置为 No pull-up and no pull-down)。

图 7.1.3 GPIO 引脚配置

使用手机控制时需要 WiFi 摄像头模块的支持。有关 ATKP 格式的说明，大家可以参 考《MiniFly 遥控器开发指南.pdf》。stabilizerTask 才是我们的重点，主要包括姿态解算和 PID 控制输出，下面我们就讲解一下姿态解算和 PID 算法流程。

## 7.2 姿态解算和 PID 算法流程图

微型四轴的姿态解算和 PID 算法流程图如图 6.3.1 所示：

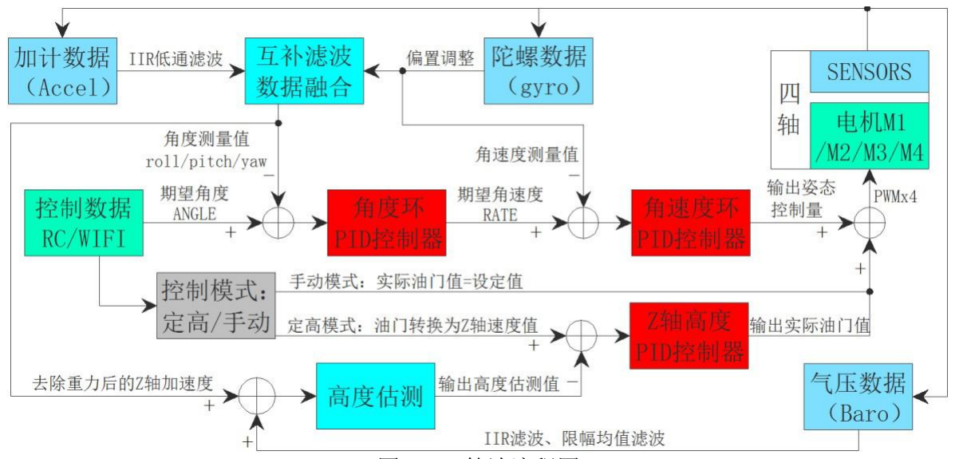
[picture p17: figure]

图 6.3.1 算法流程图
关于姿态解算，微型四轴采用互补滤波算法进行姿态解算，更新周期 500Hz。MCU 通过 IIC(模拟 IIC)读取加速计和陀螺仪数据寄存器，然后对加速计数据 IIR 低通滤波，对 陀 螺 仪 数 据 加 偏 置 调 整 ， 然 后 对 加 计 数 据 和 陀 螺 数 据 进 行 融 合 ， 输 出 姿 态 数 据 （roll/pitch/yaw）, 互补滤波算法具体内容请看 7.4 节。
角度环 PID 控制器，更新周期 500Hz。期望角度来自手机蓝牙发送的指令，测量角度 来自数据融合，期望角度减去测量角度得到偏差角度，这个偏差值作为角度环的输入，经 过角度环 PID 后输出期望角速度，角度环 PID 详细内容请看 7.4 节。
角速度环 PID 控制器，更新周期 500Hz。测量角速度来自陀螺数据，期望角速度减去 测量角速度得到一组偏差值，这组偏差值作为角速度环的输入，经过角速度环 PID 后输出 的姿态控制量，用作控制电机，角速度环 PID 详细内容请看 7.5 节。 得到实际油门值和姿态控制量数据，我们就可以把油门值和姿态控制量数据整合，整 合周期 1000Hz，然后通过控制 PWM 控制电机，从而控制四轴，关于油门值和姿态控制 量数据融合详细内容请看 6.7 节。

## 7.3 基于四元数的姿态解算互补滤波算法

微型四轴的姿态解算算法采用四元数的互补滤波算法。在一个 IMU 系统中，一般集成有 加速度计传感器、陀螺仪传感器、磁传感器等。目前常见的飞控系统中只使用一个姿态传感 器芯片，这个芯片集成了加速度计、陀螺仪以及磁传感器，四轴使用一颗 6 轴传感器芯片 MPU6050。接下来说说如何把传感器数据通过四元数和欧拉角解算成飞行器的姿态。

姿态解算关键代码如下：
void IMUupdate(float gx, float gy, float gz, float ax, float ay, float az) /*数据融合 互补滤波*/
{ float norm;
float vx, vy, vz;

float ex, ey, ez;

//四元数积分，求得当前的姿态
float q0_last=q0;
float q1_last = q1;
float q2_last = q2;
float q3_last = q3;
下面把四元数换算成方向余弦中的第三行的三个元素。vecxZ、vecyZ、veczZ 就是上一 次的欧拉角（四元数）的机体坐标参考系换算出来的重力的单位向量。

//把加速度计的三维向量转成单位向量
norm = invSqrt(ax*ax + ay*ay + az*az); ax = ax * norm; ay = ay * norm; az = az * norm;

//估计重力加速度方向在飞行器坐标系中的表示，为四元数表示的旋转矩阵的第三行
vx = 2*(q1*q3 - q0*q2); vy = 2*(q0*q1 + q2*q3); vz = q0*q0 - q1*q1 - q2*q2 + q3*q3;

ax、ay、az 是机体坐标参照系上，加速度计测出来的重力向量，也就是实际测出来的 重力向量，vx、vy、vz 是根据陀螺仪数据推算出的重力向量，它们都是机体坐标参照系上 的重力向量。
那它们之间的误差向量，就是陀螺积分后的姿态和加计测出来的姿态之间的误差。向 量间的误差，可以用向量叉积（也叫向量外积、叉乘）来表示，ex、ey、ez 就是两个重力 向量的叉积。

//加速度计读取的方向与重力加速度方向的差值，用向量叉乘计算
ex = ay*vz - az*vy; ey = az*vx - ax*vz; ez = ax*vy - ay*vx;

这个叉积向量仍旧是位于机体坐标系上的，而陀螺积分误差也是在机体坐标系，而且叉 积的大小与陀螺积分误差成正比，正好拿来纠正陀螺。（你可以自己拿东西想象一下）由于 陀螺是对机体直接积分，所以对陀螺的纠正量会直接体现在对机体坐标系的纠正。 用叉积误差来做 PI 修正陀螺零偏

//误差累积，已与积分常数相乘
exInt = exInt + ex*Ki; eyInt = eyInt + ey*Ki; ezInt = ezInt + ez*Ki;

//用叉积误差来做 PI 修正陀螺零偏，即抵消陀螺读数中的偏移量
gx = gx + Kp*ex + exInt;
gy = gy + Kp*ey + eyInt;
gz = gz + Kp*ez + ezInt;

## 四元数微分方程，其中 q0_last 、q1_last 、q2_last 、q3_last 分别为上一次的四元数值

q0、q1、q2、q3， halfT 为测量的半周期，gx、gy、gz 为陀螺仪角速度，以下都是已知 量，这里使用了一阶毕卡算法求解四元数微分方程：
//一阶近似算法，四元数运动学方程的离散化形式和积分
q0 = q0_last + (-q1_last*gx - q2_last*gy - q3_last*gz)*halfT;
q1 = q1_last + ( q0_last*gx + q2_last*gz - q3_last*gy)*halfT;
q2 = q2_last + ( q0_last*gy - q1_last*gz + q3_last*gx)*halfT;
q3 = q3_last + ( q0_last*gz + q1_last*gy - q2_last*gx)*halfT;
最后根据四元数方向余弦阵和欧拉角的转换关系，把四元数转换成欧拉角 pitch、roll、 yaw 以及去除重力加速度后的 Z 轴加速度：

//四元数规范化
norm = invSqrt(q0*q0 + q1*q1 + q2*q2 + q3*q3);
q0 = q0 * norm;
q1 = q1 * norm;
q2 = q2 * norm;
q3 = q3 * norm; out_angle.yaw += filter_gyro.z *RawData_to_Angle * 0.001f;

//四元数转欧拉角
void Get_Eulerian_Angle(struct _out_angle *angle)
{
angle->pitch = -atan2(2.0f*(q0*q1 + q2*q3),q0*q0 - q1*q1 - q2*q2 + q3*q3)*Radian_to_Angle; angle->roll = asin (2.0f*(q0*q2 - q1*q3))*Radian_to_Angle;

}

# 7.4 角度环 PID 和角速度环 PID

在讲角度 PID 之前，首先讲一下 PID 更新函数，PID 采用的标准 PID，其数学公式如

下：

将数学公式转换为 C 代码，PID 更新函数是这样的：

float pidUpdate(PidObject* pid, const float error) {
float output;
pid->error = error; | pid->integ
+= pid->error * pid->dt; | if (pid- >integ > pid->iLimit)

{
pid->integ = pid->iLimit;
}
else if (pid->integ < pid->iLimitLow)
{
Pid->integ = pid->iLimitLow; } pid->deriv = (pid->error - pid->prevError) / pid->dt;

pid->outP = pid->kp * pid->error; pid->outI =
pid->ki * pid->integ; pid->outD = pid->kd * pid- >deriv; output = pid->outP + pid->outI + pid->outD; pid->prevError =

pid->error; return output;

PidObject 为 PID 对象结构体数据类型，第一个参数为将被更新的 PID 结构体对象， 第二个参数则是偏差（期望值-测量值），积分项为偏差对时间的积分，微分项则是偏差对 时间的微分，然后函数里面有三个参数 pid->kp，pid->ki，pid->kd 分别指的是该 pid 对象 的比例项，积分项和微分项系数，每个 pid 对象都有属于自己的 PID 系数，PID 初始化 pid 对象的时候会设定一组默认的系数，同时这组系数是可以调整的，我们常说的 PID 参 数整定，其实就是调整这组系数，让它满足你的系统。
接下来我们说说角度环 PID，其函数原型如下
void Control_Angle(struct _out_angle *angle,struct _Rc *rc)
{
static struct _out_angle control_angle; static struct _out_angle last_angle;

if(rc->ROLL>1490 && rc->ROLL<1510) rc->ROLL=1500;
if(rc->PITCH>1490 && rc->PITCH<1510) rc->PITCH=1500;
if(rc->AUX1>1495 && rc->AUX1<1505) rc->AUX1=1500;

if(rc->AUX2>1495 && rc->AUX2<1505)
rc->AUX2=1500; control_angle.roll = angle->roll - (rc->ROLL -1500)/13.0f + (rc->AUX2 -1500)/100.0f; control_angle.pitch = angle->pitch - (rc->PITCH -1500)/13.0f - (rc->AUX1 -1500)/100.0f;

if(control_angle.roll > angle_max) //ROLL roll.integral += angle_max; if(control_angle.roll < -angle_max) roll.integral += -angle_max; else

roll.integral += control_angle.roll; if(roll.integral > angle_integral_max) roll.integral = angle_integral_max; if(roll.integral < -angle_integral_max) roll.integral = -angle_integral_max; if(control_angle.pitch > angle_max)//PITCH pitch.integral += angle_max; if(control_angle.pitch < -angle_max) pitch.integral += -angle_max; else pitch.integral += control_angle.pitch;

if(pitch.integral > angle_integral_max) pitch.integral = angle_integral_max; if(pitch.integral < -angle_integral_max) pitch.integral = -angle_integral_max;

if(rc->THROTTLE<1200)//油门较小时，积分清零

{
roll.integral = 0;
pitch.integral = 0;
}
roll.output = roll.kp *control_angle.roll + roll.ki *roll.integral + roll.kd *(control_angle.roll -last_angle.roll );
pitch.output = pitch.kp*control_angle.pitch + pitch.ki*pitch.integral + pitch.kd*(control_angle.pitch-last_angle.pitch);
last_angle.roll =control_angle.roll;

last_angle.pitch=control_angle.pitch;
}

attitude_t 是一个姿态数据结构类型，函数参数 actualAngle 是一个结构体指针，指向实

## 际角度结构体变量（数据融合输出值）state->attitude, desiredAngle 指向期望角度结构体变 量（设置的角度）attitudeDesired，outDesiredRate 则是角度环的输出，指向期望角速度结构

体变量 rateDesired。此处 PID 更新的分别是角度环的 3 个 pid 对象结构体 ，输入偏差为

## 期望角度减去测量角度（actualAngle- desiredAngle）。YawError 处理那段，是为了快速计

算并限制其范围在-180°到+180°。
然后是角速度环 PID，其函数原型如下：
/* 角速度环 PID */ void Control_Gyro(struct _SI_float *gyro,struct _Rc *rc,uint8_t Lock)

{
static struct _out_angle control_gyro; static struct _out_angle last_gyro;

int16_t throttle1,throttle2,throttle3,throttle4; if(rc->YAW>1400 && rc->YAW<1600) rc->YAW=1500;
if(rc->AUX3>1495 && rc->AUX3<1505) rc->AUX3=1500; control_gyro.roll = -roll.output - gyro->y*Radian_to_Angle; control_gyro.pitch = pitch.output - gyro->x*Radian_to_Angle;

if(rc->AUX4 & Lock_Mode) control_gyro.yaw = - gyro->z*Radian_to_Angle - (rc->AUX3 -1500)/100.0f;//锁尾模式

else
control_gyro.yaw = -(rc->YAW-1500)/2.0f - gyro->z*Radian_to_Angle + (rc->AUX3 -1500)/50.0f;//非

锁尾模式
if(control_gyro.roll > gyro_max) //GYRO_ROLL
gyro_roll.integral += gyro_max;
if(control_gyro.roll < -gyro_max) gyro_roll.integral += -gyro_max; else gyro_roll.integral += control_gyro.roll;

if(gyro_roll.integral > gyro_integral_max) gyro_roll.integral = gyro_integral_max; if(gyro_roll.integral < -gyro_integral_max)

gyro_roll.integral = -gyro_integral_max; if(control_gyro.pitch > gyro_max)//GYRO_PITCH gyro_pitch.integral += gyro_max; if(control_gyro.pitch < -gyro_max) gyro_pitch.integral += -gyro_max; else gyro_pitch.integral += control_gyro.pitch;

if(gyro_pitch.integral > gyro_integral_max) gyro_pitch.integral = gyro_integral_max; if(gyro_pitch.integral < -gyro_integral_max) gyro_pitch.integral = -gyro_integral_max; gyro_yaw.integral += control_gyro.yaw; if(gyro_yaw.integral > gyro_integral_max) gyro_yaw.integral = gyro_integral_max; if(gyro_yaw.integral < -gyro_integral_max) gyro_yaw.integral = -gyro_integral_max;

if(rc->THROTTLE<1200)//油门较小时，积分清零

{ | gyro_yaw.integral = 0; | }
gyro_roll.output = gyro_roll.kp *control_gyro.roll + gyro_roll.ki *gyro_roll.integral + gyro_roll.kd *(control_gyro.roll -last_gyro.roll );
gyro_pitch.output = gyro_pitch.kp*control_gyro.pitch + gyro_pitch.ki*gyro_pitch.integral + gyro_pitch.kd*(control_gyro.pitch-last_gyro.pitch);
gyro_yaw.output = gyro_yaw.kp *control_gyro.yaw + gyro_yaw.ki *gyro_yaw.integral + gyro_yaw.kd *(control_gyro.yaw -last_gyro.yaw );
last_gyro.roll =control_gyro.roll;
last_gyro.pitch=control_gyro.pitch;
last_gyro.yaw =control_gyro.yaw;
if(rc->THROTTLE>1200 && Lock==0){
throttle1 = rc->THROTTLE - 1050 + gyro_pitch.output + gyro_roll.output - gyro_yaw.output; throttle2 = rc->THROTTLE - 1050 + gyro_pitch.output - gyro_roll.output + gyro_yaw.output; throttle3 = rc->THROTTLE - 1050 - gyro_pitch.output + gyro_roll.output + gyro_yaw.output; throttle4 = rc->THROTTLE - 1050 - gyro_pitch.output - gyro_roll.output - gyro_yaw.output; }
else{
| throttle1=0;

throttle2=0;
throttle3=0;
throttle4=0;
}
Motor_Out(throttle1,throttle2,throttle3,throttle4);
}

## Axis3f 是一个 3 轴数据结构体类型，control_t 是控制数据结构体类型。参数 actualRate 指 向 3 轴 陀 螺 结 构 体 变 量 sensors->gyro ， desiredRate 则 指 向 角 度 环 PID 的 输 出 rateDesired， control_t 则指向 control 结构体变量，control 结构体包含了角速度环的输出数

据—姿态控制量数据，这个数据用作控制电机。此处 PID 更新的分别是角速度环的 3 个 pid 对象结构体 ，输入偏差为期望角速度减去测量角速度（actualRate- desiredRate）， pidOutLimit 函数用作限制姿态控制量的调整范围（-32768~+32767），防止调整量过大，难 以控制。

## 7.5 姿态控制量和油门值整合

微型四轴为 X 模式飞行，电机转向和姿态解算正方向（箭头指示正方向）如图 6.7.1 所示：

图 6.7.1 电机转向和姿态解算方向
rc->THROTTLE 为油门控制量，这个值增大四轴升高，减小则下降。rc->ROLL，rc->PITCH， rc->YAW 为 PID 输出的姿态控制量。油门控制量和姿态控制量整合后控制电机，整合代码在 power_control.c 文件的函数 powerControl()中实现，代码如下：
void RC_Limit(struct _Rc *rc)
{
rc->THROTTLE = (rc->THROTTLE<=1000)?1000:rc->THROTTLE; rc->THROTTLE = (rc->THROTTLE>=2000)?2000:rc->THROTTLE; rc->PITCH = (rc->PITCH<=1000)?1000:rc->PITCH; rc->PITCH = (rc->PITCH>=2000)?2000:rc->PITCH; rc->ROLL = (rc->ROLL<=1000)?1000:rc->ROLL; rc->ROLL = (rc->ROLL>=2000)?2000:rc->ROLL;

rc->YAW = (rc->YAW<=1000)?1000:rc->YAW; rc->YAW = (rc->YAW>=2000)?2000:rc->YAW; rc->AUX1 = (rc->AUX1<=1000)?1000:rc->AUX1; rc->AUX1 = (rc->AUX1>=2000)?2000:rc->AUX1; rc->AUX2 = (rc->AUX2<=1000)?1000:rc->AUX2; rc->AUX2 = (rc->AUX2>=2000)?2000:rc->AUX2; rc->AUX3 = (rc->AUX3<=1000)?1000:rc->AUX3; rc->AUX3 = (rc->AUX3>=2000)?2000:rc->AUX3;

}

如图 6.7.1 所示，微型四轴右上角为 M1 机臂，在代码中对应电机为 motorPWM.m1，然 后顺时针依次为 M2，M3，M4。如果四轴受外力干扰导致 PITCH 轴向前倾斜 3 度，那么 M1 和 M4 需要提高升力，M2 和 M3 减小升力来恢复平衡状态，所以有以下规则： Roll 方向（向右为正）旋转，为了恢复平衡，则 M3 和 M4 同侧出力，M1 和 M2 反
向出力（m1 和 m2 的 Roll 为-，m3 和 m4 的 Roll 为+）;
Pitch 方向（向前为正）旋转，为了恢复平衡，则 M2 和 M3 同侧出力，M1 和 M4 反
向出力（m1 和 m4 的 Pitch 为-，m2 和 m3 的 Pitch 为+）;
Yaw 方向（逆时针为正）旋转，为了恢复平衡，则 M1 和 M3 同侧出力，M2 和 M4
反向出力，（m2 和 m4 的 Yaw 为-，m1 和 m3 的 Yaw 为+）;

## bool 型变量 motorSetEnable，为 true，使能手动设置电机占空比，这样可以

方便单独调试某几个电机，默认不使能。
motorsSetRatio()当然就是设定对应电机定时器通道占空比的函数了，设定 的占空比作用到 MOS 管，然后控制电机，从而控制四轴。

## 7.6 蓝牙无线串口通讯协议

## APP 和飞控之间的通信协议使用了 MWC 飞控协议(MSP, Multiwii Serial Protocol)，详见 MSP 协议格式。 (http://www.multiwii.com/wiki/index.php?title)

MWC 协议规定了飞控和上位机（或者手机 APP）信息交流的基本格式。

## MWC 具体实现，可以查看 Android APP 源代码中的 Protocol.java 文件。

串口通信采用 UART 通讯方式，数组名为 Bluetooth_RXDATA，一次发送八个 字节，低八位读取。若发送的位数超过 8 位，则使用两个数组元素来存放一个通 道的数据。

通信协议格式如下所示：

串口数组 | 作用
Bluetooth_RXDATA[0] | 数据校验，内容为$

Bluetooth_RXDATA[1] | 数据校验，内容为 M
Bluetooth_RXDATA[2] | 发送标志， 若为四轴发送给上位机，则内容为> 若为上位机发送给四轴，则内容为<
Bluetooth_RXDATA[3] | 串口长度，用于校验
Bluetooth_RXDATA[4] | 功能桢标志
Bluetooth_RXDATA[5] ~Bluetooth_RXDATA[20] | 取决于功能帧的标志

## 7.7 手机控制软件框架

## Android 手机控制软件采用 Android Studio 开发，并采用最新版本 29 版本的 Android SDK，操作系统最高支持 Android 9.0，最低支持 Android 4.3.0。BLE 技术

需要 Android4.3 及以上系统支持。源码采用 Java 语言编写而成，通过使用 Bluetooth BLE4.0 协议，可通过 Android 手机实现近距离控制配套的微型四轴。

源码的主要 java 代码文件在

# 8. 微型四轴二次开发

# 8.1 MDK 开发环境搭建

我们微型四轴源码工程是基于 MDK5 开发，下面我们先安装这个软件。MDK5 安装源 文件在微型四轴资料中有提供，如下图 7.1.1 所示。

图 7.1.1 MDK 安装源文件目录
MDK 安装过程就不详细说明，安装前先看“安装过程.txt”。安装完 MDK 软件之后 还需要安装芯片包（图 7.1.1 中.pack 文件），直接双击芯片包文件即可安装（先安装 MDK 软件）。所有都安装完成之后打开微型四轴源码工程如下图 7.1.2 所示。

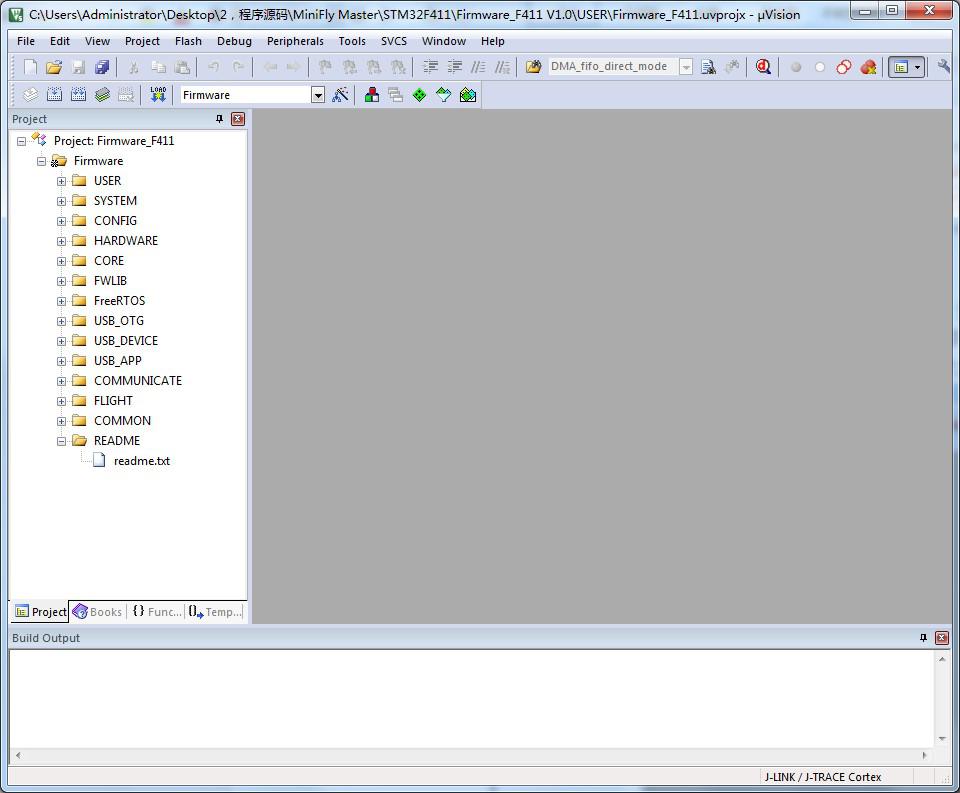
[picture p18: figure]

图 7.1.2 源码工程示图

# 8.2 CubeMX 开发环境搭建

STM32CubeMX 是 STM32 芯片图形化配置工具， 允许用户使用图形化向导生成 C 初始化 代码，可以大大减轻开发工作，时间和费用。STM32CubeMX 几乎覆盖了 STM32 全系列芯片。

目前，ST 公司已基于 STM32CubeMX 的基础上，融入 eclipse 开发生态环境，通过 arm 交 叉编译器设计出新一代嵌入式开发 IDE——STM32CubeIDE。

首先安装 Java 运行环境，双击 JavaSetup8u151 在线下载安装包，全部点击默认安装 即可。（需要注意，STM32CubeMX 的 Java 运行环境版本必须是 V1.7 及以上，如果你 的 电 脑 安 装 过 V1.7 以 下 版 本 ， 请 先 删 掉 后 重 新 安 装 最 新 版 本 ） ， 然 后 安 装 STM32CubeMX，直接双击 STM32CubeMX 安装包，默认安装在 C 盘，可以改变安装路径。安 装之后打开该软件，接下来我们安装 STM32 库，点击 Help->Install New Libraries 或者 按快捷键 ALT + U。这里我们推荐使用离线下载（在线下载速度较慢而且不支持断点续传 功能），也可使用我们提供的 STM32G030 系列的库函数。注意：固件库的固件要与开发板 的主控型号对应，否则无法使用。

## 8.3 固件下载

首先我们给下载器安装驱动。下载器驱动文件路径：“微型四轴资料\ST LINK 驱动及 教程\STLINK 驱动”。驱动安装过程这里就不详细说明，安装完成后将 USB 线连接好下载

器并插入电脑，然后打开设备管理器，在通用串行总线控制器中即可找到 ST-Link driver， 如下图 7.2.1 所示。

图 7.2.1 下载器驱动
然后将下载器连接到四轴，下载器通过 4Pin 线连接到四轴，如下图 7.2.2 所示。

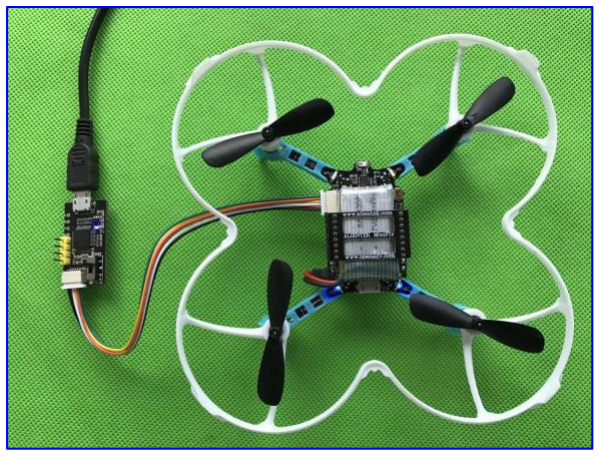
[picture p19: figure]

图 7.2.2 下载器连接图
然后打开程序源码。驱动安装完成之后，我来看看程序源码文件。程序源码目录树如下

图 7.2.3 程序源码目录树
编译固件并下载。解压 CubeMX_Code.zip 并打开程序工程，点击编译，等待编译完成再 点击下载。操作步骤如下图 7.2.5 所示。下载完成后如图 7.2.6 所示。所有程序源码下载都可

以按照此方法执行，这里就不重复。

图 7.2.4 固件下载操作步骤示图

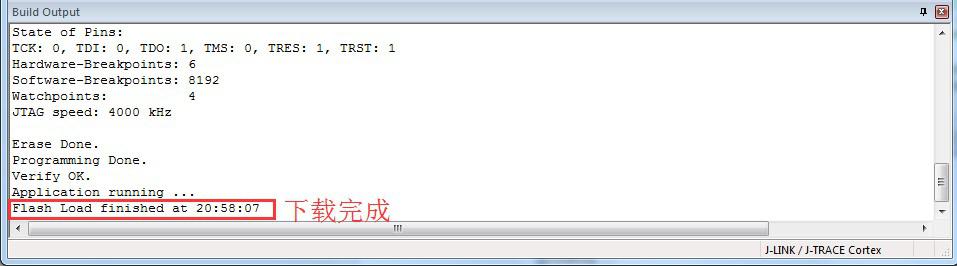
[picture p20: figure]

图 7.2.5 程序下载完成示图
提示： 下载时，芯片必须是上电状态。

## 8.4 安卓地面站使用

我们微型四轴兼容了功能强大的 MWC 地面站，该软件路径：“微型四轴资料\匿名四轴上 位机”。MWC 地面站支持很多通信方式，这里我们使用的是蓝牙无线串口方式通信。下面介 绍怎么使用匿名科创地面站查看飞控姿态，显示数据波形及 PID 调试。

第一步，打开四轴飞行器，使用杜邦线将 USB-TTL 串口连接至蓝牙无线传输模块，而 后将 USB-TTL 无线串口模块连接至电脑端，在设备管理器中找到端口号。注意：使用遥控 器和地面站通信时，只有四轴是开机状态才有数据上传。
第二步，打开软件选择串口通信

图 7.3.1 串口通信设置图
打开软件后点击左边一列图标的程序设置，即可显示程序设置界面，如图 7.3.1 所 示。我们选择通信连接方式为 COM 方式，然后选择端口号，设置波特率为 500000，最后 点击右下角的打开连接，即可通信。当有数据上传时，RX:显示接收到数据的个数。 第三步，查看飞控状态

图 7.3.2 飞控状态图
点击左边一列图标的飞控状态即可显示飞控状态界面，如图 7.3.2 所示。飞控状态显示 主要包括当前四轴姿态（PIT\ROL\YAW）、接收机（遥控器控制数据）、电机输出 （PWM）、传感器原始数据（ACC\GYR\MAG）、气压高度（单位 cm）、电池电压。飞 行模式和 GPS 信息功能未使用。
第四步，查看数据波形

图 7.3.3 数据波形图
点击左边一列图标的数据波形即可显示数据波形界面，如图 7.3.3 所示。首先选中我 们要显示的数据，再点击飞控数据即可显示数据波形。
第五步，PID 调试

## 图 7.3.4 PID 调试图

点击左边一列图标的飞控设置即可显示飞控设置界面，如图 7.3.4 所示。飞控设置包 括 PID 设置、飞行模式设置、传感器校准，这里我们只使用了 PID 设置的功能。读取飞 控：读取四轴当前 PID 参数。写入飞控：将显示的所有 PID 参数写入到飞控。恢复默认 值：将四轴 PID 参数恢复成出厂默认值。这里我们总共使用了 7 组 PID，分别是 roll 速 率、pitch 速率、yaw 速率、roll 角度、pitch 角度、yaw 角度、高度位置。
注意：显示的 PID 数值是实际数值的 10 倍。由于地面站 PID 数据传输只能是 int16 类 型不能浮点型，所以将实际数值乘以 10 再上传，同时写入时也除以了 10。

# 8.5 微型四轴 PID 调试

众所周知 PID 调试是四轴最难的一部分，也是最核心的一部分，PID 参数是否合理直 接影响四轴飞行的效果。下面就介绍一下我们微型四轴的 PID 调试方法。 第一步，修改 G030 固件代码

图 7.4.1 PID 控制函数示图

打开 CubeMX_Code 源码文件夹，打开 MDK-ARM/CubeMX_Code.uvprojx 工程文件，PID 控制器的内外环函数位于 Application/User 文件夹下的 Control.c，如上图所示。修改后 编译固件并下载到四轴。 第二步，搭建四轴调试平台

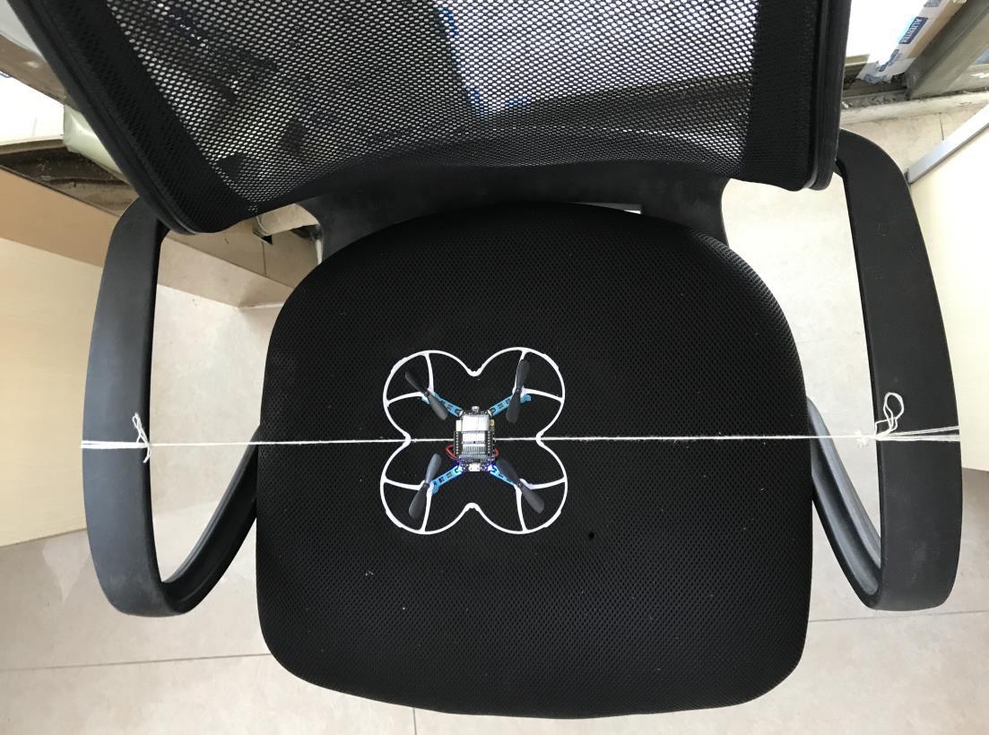
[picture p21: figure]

## 图 7.4.2 MiniFly 四轴调试平台搭建示图

如上 7.4.2 所示，使用两条细绳一端拴住微型四轴用于固定电池的排针，另一端拴住椅 子的两端扶手，并保证微型四轴可以 360 度旋转不会碰到椅子面。绳子拴住的排针最好是四 轴中间位置的排针，排针不在机身中间，所以机身中间的排针不一定是排针中间的那一根。 最好选择扶手较高的椅子，这样机身离椅子面足够的距离排风。注意：四轴开机后一直晃动 陀螺仪是校准不通过的，需要使用物体卡住使其静止等待校准通过。 第三步，遥控器连接上位机

## 图 7.4.3 PID 初始设置示图

使用 USB 线将遥控器连接到上位机，点击右下角打开连接，然后并打开飞控设置， 设置自稳 ROL 和自稳 PIT 的 P 为 10，点击写入飞控，上方会显示“PID 数据 6”发送成 功，如图 7.4.3 所示。串级 PID 调试一般先调内环（速率环），所以先将外环（角度环） PID 的 P 设置为 1，I 和 D 设置为 0。注意：上位机显示是放大了 10 倍，后面的调试值 均是上位机显示的值。 第四步，调内环 pitch 和 roll 的 P

设置遥控器为手动模式，然后解锁长按 KEY_R 键进入调试界面。按照第三步操作后， 我们给内环 ROL 速率和 PIT 速率的 P 同时设置一个值，然后推动油门至 50 左右观察并记 录现象。下面是测试我们不同 P 的值和对应的现象：
P = 10 时，四轴乱晃无法固定于某一个角度，用手轻轻干扰四轴会绕绳子旋转，说明 P 值太小，力度不够。
P = 100 时，四轴晃动幅度减小但还是无法固定于某一个角度，用手轻轻干扰四轴还会 绕绳子旋转，说明 P 值还是太小，力度不够。
P = 1000 时，四轴已经不晃动了，用手轻轻干扰明显感觉有回复力，说明 P 值已经慢 慢趋向理想值。
P = 5000 时，四轴机身晃动严重已经震荡，说明 P 值已经过大，由此可确定理想的 P

## 值应该在 1000~5000 范围内。

P = 2500 时，四轴不晃动并且能固定在某一个角度了，机身也不震荡，用手去干扰能 感觉到明显的回复力。说明 P 值已经很接近理想值了。
P = 3500 时，四轴机身轻微晃动说明已经轻微震荡，用手去干扰能感觉到很强的回复 力。说明 P 值已经稍大于理想值了。
P = 3200 时，四轴没有晃动，用手去干扰能感觉到很强的回复力并有点晃动。说明 P 值就是我们的理想值了，晃动问题后期可以通过加点 D 抑制。 第五步，调内环 pitch 和 roll 的 D

根据第四步内环 P 已经调节好，但如果四轴受到干扰则会震荡，说明稳定性不好，这时 我们就需要通过加 D 来增强稳定性。按照第四步的操作方法，设置 P 值为 3200，,测试不同 的 D 值对应的现象：
D=10 时，用手去干扰四轴，能感觉到很强的回复力并有点晃动，说明 D 值有点小， 抑制不了干扰。
D=100 时，用手去干扰四轴，能感觉没有晃动了但四轴需要长时间才能回复到水平， 说明 D 值太大了，抑制了 P 的调整。
D=50 时，用手去干扰四轴，能感觉没有晃动了四轴也能较快回复到水平，说明 D 值 接近理想值了。
就这样我们暂时把 D 值调好了，因为后面整机试飞时可能还会调节 D 值，这里先不 用精确调节至某一个值。 第六步，调外环 pitch 和 roll 的 P

内环调好了，下面我们开始调外环。外环的主要作用是控制四轴姿态响应快慢，下面我 们测试不同的 P 值，观察四轴的响应速度。按照前面操作方法，我们测试 P 值和现象如下： P=10 时，方向摇杆往前打到最大，发现四轴慢慢倾斜，最终达到设定角度。响应速度 不够快，说明 P 太小了。
P=100 时，方向摇杆往前打到最大，四轴瞬间倾斜了达到设定角度，而且力量很大。 说明 P 值太大了。
P=50 时，方向摇杆往前打到最大，四轴较快的达到设定角度，不是很快也不是很慢。 说明 P 值是我们理想值了。 第七步，调内环 yaw 的 PID

调节内环 yaw 的 PID 前需将第一步注释掉的 ENABLE_PID_TUNING 宏定义重新注释回 来，并且编译下载至四轴。然后设置 yaw 外环 P 为 10，内环 P 设定为某一个值，慢慢 推油门让四轴起飞至水平，推油门摇杆时不要向左或向右打到航向角。飞至水平后，推油 门至 50，然后用手轻轻向左边或向右拨动四轴，感受四轴的回复力，并且听电机的声音。 下面是我们设置不同内环 P 的值时对应的现象：
当 P=10 时，四轴几乎没有回复力，受干扰后左右摆晃，电机声音差异不大。说明 P 值太小了，没有修正的回复力。
当 P=100 时，四轴有一点点回复力，受干扰后左右摆晃，电机声音差异不大。说明 P 值还是太小。
当 P=1000 时，四轴有明显的回复力，受干扰后不会摆晃，电机声音差异很大。说明 P 值接近理想值了。
当 P=5000 时，四轴有明显的回复力，受干扰后两个电机停止转动，电机声音差异非 常大。说明 P 值已经太大了。
跟以上调试现象和经验我们最终选定 P 值为 1200，然后再逐渐添加一点了积分 I，没 有添加 D。内环的反馈是陀螺仪，航向角也是由陀螺仪积分而得，陀螺仪在四轴飞行过程有 高频干扰，高频干扰使得 D 具有相反作用，所以我们没有添加 D。 第八步，调外环 yaw 的 PID

调节外环 yaw 的 P 和调节外环 pitch\roll 的 P 方法一样，主要是调节四轴的受控制的响应 速度。给外环 yaw 的 P 设定一个值然后推油门和航向角，感受四轴旋转的快慢。这里我们 选定 P 的值为 100。

第九步，手动试飞

经过以上步骤调试，四轴基本可以手动飞行了，松开绳子测试手动飞行。飞行过程中如 果在无风条件下发现四轴晃动说明内环 pitch 和 roll 的 P 值大了，这时可以通过减小 P 或增 加 D 来抑制晃动。如果发现航向角受外力干扰不能快速回复到原本状态，这可能是内环 yaw 的 P 太小了，需要增加 P。如果发现飞行过程会慢慢自旋，说明 yaw 的 I 太大了，需要减 小 I 值。经过以上反复调试，我们最终确定我们 MiniFly 四轴 PID 参数如下图 7.4.4 所示：

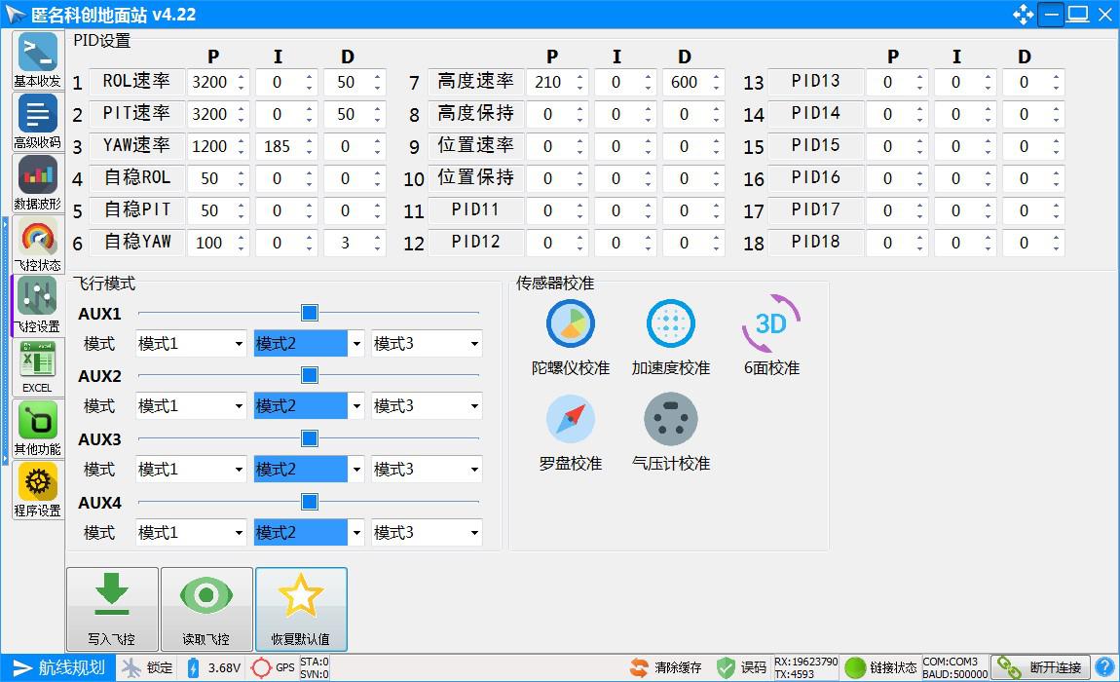
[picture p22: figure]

## 图 7.4.4 微型四轴 PID 参数

第十步，调定高的 PID

定高 PID 调节是比较揪心的，调试过程我们按照正常的 PID 调试方法先调 P 再调 I 最后调节 D，反复调试发现根本行不通，四轴依旧很难定在一定高度范围内。后来经过分 析，我们发现使用气压计定高，气压数据有很大的滞后性，并且四轴飞行过程垂直向下的风 也会干扰气压读数。所以我们调试时不管怎么调节 P，出现的现象是要么慢慢的上升或慢 慢的下降，要么快速上蹿下跳，根本不受控制。后来我们根据 PID 理论中 D 有抑制超调和 干扰的作用，索性把 D 也先加上一点点，果然有效果，四轴上蹿下跳没那么厉害了。继续 增加 D 四轴更加稳定了，当 D 增加到很大时，我们发现，推动油门四轴不怎么受控制了， 说明 D 值太大了将 P 的作用都抑制了。反复调试后，我们最终选定 PID 的值为
210,0,600。 总结

PID 三项的的意义：P 是系统平衡的回复力； I 是消除误差，有辅助 P 的作用；D 是 阻尼，抑制超调和干扰的作用。调试时一般先调节 P 找到临界震荡的 P 值，然后减小一点 P 值，增加 I 值消除静态误差，最后增加 D 值抑制干扰。要不要加 I 和 D 需根据实际情 况而定。调试定高 PID 时，需要 P 和 D 同时调。PID 调试是比较繁琐的事情，需要耐心 观察现象并分析原理。

# 9. 微型四轴开发常见问题

## 9.1 STM32 虚拟串口问题

通常驱动安装失败，打开设备管理器，可以看到如下图 1.1 所示：

图 1.1 虚拟串口驱动安装失败示图
正确安装 STM32 虚拟串口驱动步骤如下：
安装资料包里的 VCP_V1.4.0_Setup.exe，这个驱动在资料包”3，配套软件 3， STM32 USB 虚拟串口驱动”文件夹内，安装完成，在如下路径可以看到如图 1.2 所示：

图 1.2 VCP_V1.4.0_Setup.exe 安装完成示图

退出 360 等安全软件，并安装虚拟串口补丁，补丁路径如下图 1.3 所示：然后双击运 行 “双击这个.bat”, 因为部分系统缺少配置文件，所以需要使用.bat 复制配置文件到系 统文件夹里。

图 1.3 安装虚拟串口补丁示图

在下图的路径下，运行 dpinst_amd64.exe 或 dpinst_x86.exe（根据自己系统位数选 择）如图 1.4 所示。安装成功后如下图 1.5 所示。 图 1.4 手动执行 dpinst_amd64.exe

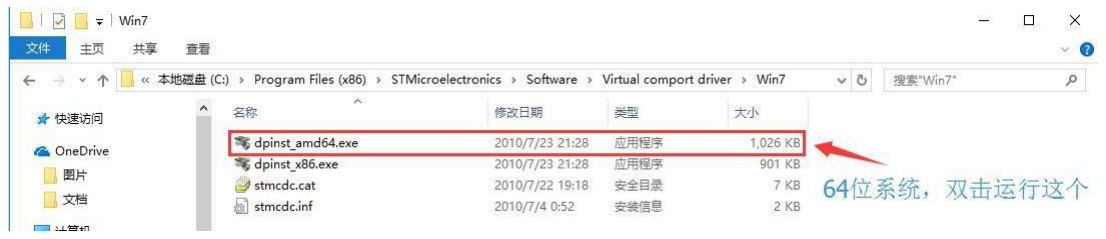
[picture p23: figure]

图 1.5 虚拟串口驱动安装成功示图

USB 连接四轴或遥控器，在设备管理 端口可以看到如下图 1.6 所示。 图 1.6 成功安装虚拟串口

驱动安装成功后，插上 USB，虚拟串口用不了，则检查下 USB 线是否接好，甚至可以换 一根 USB 线试试。

## 9.2 CubeMX 代码生成问题

注意：CubeMX 在重新生成代码后，会覆盖/* USER CODE ....... BEGIN */和/* USER
CODE ....... END */以外的区域，区域外的代码在重新生成后会被删除！

## 该工程文件由 STM32CubeMX V5.5.0 版本生成，打开 ioc 工程文件需要升级至 5.5.0 及

以上版本。

用户自己添加的 xxx.c 文件，在 CubeMX 重新 Generate 文件时，不会被删掉。 CubeMX 只是重新生成了例如 eth.c，gpio.c 之类的文件，不会把用户自己添加的文件删 掉。

然而在 keil 工程里却被删掉，因此需要重新添加。为了避免重复添加用户自己的源代 码和头文件，可以进行如下操作：

## 1. 打开 mdk 工程

2. 打开 cubemx 工程，也就是 ioc 后缀文件
3. 进行你的配置，重新生成 mdk 工程（生成的之前 mdk 工程要打开）
4. 点击最小化的 mdk，然后可以看到提示框

更新 xxx.c 文件，选择是

更新 xxx.h 文件，选择是

最重要的一步，提示更新工程文件，选择否

好了，现在芯片配置的代码已经同步过来了，工程文件还是用原来的，添加的文件就 还在了，重新编译，ok。

## 9.3 四轴飞行过程往一边偏

如果偏飞得厉害，先检查遥控器微调值是否为 0，如果不为零，就先调整为 0 再试飞 看飞行效果。如果通过微调的方式不能纠正偏飞问题，那就是其他原因所致。

电机坏了，电机坏了也分好几种情况，比如像图 2.1 那种情况，电机蓝色底座脱离或 者脱落，这种情况导致电机输出动力减弱，甚至有烧坏 MOS 管的可能；还有像图 2.2 那 种情况，电机输出轴弯曲，输出轴弯曲，装上桨叶转动起来就会因为不平衡产生很大的 震动，震动的直接结果就是导致传感器读数据精度变差甚至错误；还有可能是电机长时 间工作，轴承或者电刷磨损厉害，导致动力减弱，因为有刷电机是有寿命的，按正常使 用来说，这个电机还是有几个月寿命的。对于这种电机坏了的情况，我们只需要换上新 的电机即可。

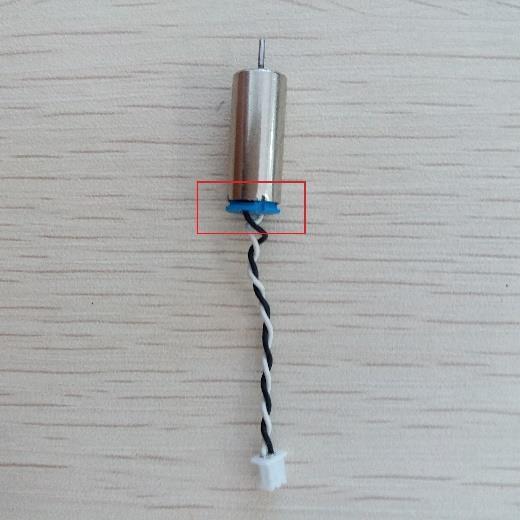
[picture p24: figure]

图 2.1 电机蓝色底座脱离 | 图 2.2 电机中心转轴弯曲

注意：

对于如图 2.1 电机底座脱离的情况，电机就不能再使用了，只能更换新电机，因为电 机在这种状态下，不但没有动力输出，甚至会导致 MOS 管烧掉或者短路，MOS 短路 后，上电电机不受控制直接就转起来了，如果 MOS 管烧掉那就得重新焊接了。

偏飞也有可能是桨叶不平衡所致，因为空心杯转速高，装上不平衡桨叶高速转动， 就会产生很大震动，过大的震动导致传感器度数精度降低甚至错误。怎么看桨叶是否平 衡呢？最直接的就是看桨叶是否磨损，变形以及残缺等。如果这种情况，直接换上新的 桨叶即可，注意桨叶是有正反的。

偏飞也有可能是信号干扰导致，信号干扰导致四轴接受不到控制信号，从而出现偏 飞的情况，如何判断干扰呢？在可控制范围内，遥控器控制四轴飞行，无干扰的时候， 遥控器蓝色通讯指示灯常亮；有一点点干扰（不会影响飞行）的时候，遥控器红色指示 灯偶尔闪烁一下，蓝色指示灯基本还是常亮；当干扰变严重，遥控器红色指示灯常亮， 这时候四轴基本接收不到遥控器控制信号了，偏飞，乱飞的可能性就很大了。

## 9.4 四轴定高飞行，高度定不住

定高是讨论比较多的一个话题，当然主要讨论的就是定高效果的问题，有不少用户反 映定高效果差的问题，比如定高飞不起来，响应缓慢，飞起来上窜下窜等，反正就是有 很多问题，当然这里面不排除硬件（电机，桨叶）的问题以及软件（PID）问题。

1.1 版本固件使用串级(位置环+速度环)PID 的方式控制定高，增加稳定性的同时提高 了响应速度，定高稳定性也不会受到自重影响。如果定高效果还是很差，那么我们检测 下是否是硬件的问题。

## 9.5 下载器不能下载调试代码

如果下载器开关设置好了，下载线 2 端也对接好了，还是不能下载，有可能是如下 原因：
编译出错，提示代码超过 32K，这种情况是因为 MDK 未破解，这种情况只需要百度 一下 MDK 破解。

编译或者下载提示找不到芯片，应该是 MDK 安装之后没有安装相应芯片的 pack 包。 请安装芯片型号对应的 Pack 包。

下载或者调试出现如图 5.1 所示的提示：

图

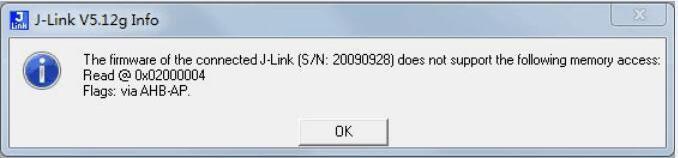
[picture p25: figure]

5.1 驱动问题提示

这种情况需要替换一下 jlink 驱动，用我们提供的驱动替换 MDK 安装路径下对应的驱 动，替换之前可以先将原来的驱动备份一下。在微型四轴资料包里找到“Segger.zip”，解压 出来，然后替换 MDK 安装目录下的 Segger 文件夹，如图 5.2 和 5.3 所示：

图 5.2 新的驱动包

图 5.3 替换掉原来的文件夹

注意 ：

调试微型四轴时，请务必接上电池四轴供电，不能用下载器的电源给四轴供电并调 试，下载器带载能力较弱，只使用它给微型四轴供电调试可能导致下载器烧掉。

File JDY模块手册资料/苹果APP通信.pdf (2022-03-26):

苹果 APP 下载：在苹果商店输入 LightBlue 安装

1、打开 APP 后搜索到 JDY-32


2、选择 JDY-32-LE 进入连接界面


3、选择 FFE1，进入 FFE1 界面


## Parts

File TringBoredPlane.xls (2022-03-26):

Comment | Description | Value | Footprint | Designator | LibRef | Quantity | Pins
STM32G030K |  |  | LQFP32M | U1 | STM32G030K | 1 | 32
Res | Resistor | 1K | 1206M | R1, R2, R3, R4 | Res | 4 | 2
Res | Resistor | 1K | LC-0805_R | R5, R6 | Res | 2 | 2
Res | Resistor | 4k7 | LC-0805_R | R7, R8 | Res | 2 | 2
NMOS |  |  | SOT23-3M | Q1, Q2, Q3, Q4 | NMOS | 4 | 3
MPU6050 |  |  | QFN4*4-24M | U2 | MPU6050 | 1 | 14
ME6206Axxx |  |  | sot89m | U3 | ME6206Axxx | 1 | 3
LED_Green |  |  | D0805M | D1, D2 | LED | 2 | 2
LED_Red |  |  | D0805M | D3, D4 | LED | 2 | 2
Dio |  |  | DO-214ACM | D5, D6, D7, D8 | Dio | 4 | 2
Connector-3 |  |  | XH2.54TH-3 | SW | Connector-3 | 1 | 3
Connector-2 |  |  | XH2.54TH-2 | BET, M1, M2, M3, M4 | Connector-2 | 5 | 2
Connector5 |  |  | 2.54th5 | BlueTooth | Connector5 | 1 | 5
Cap | Capacitor | 1uF | 1206m | C6, C7 | Cap | 2 | 2
Cap | Capacitor | 2.2nF | 1206m | C5 | Cap | 1 | 2
Cap | Capacitor | 10nF | 1206m | C3 | Cap | 1 | 2
Cap | Capacitor | 100nF | 1206m | C1, C2, C4 | Cap | 3 | 2

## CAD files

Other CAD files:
教育无人机.dwg

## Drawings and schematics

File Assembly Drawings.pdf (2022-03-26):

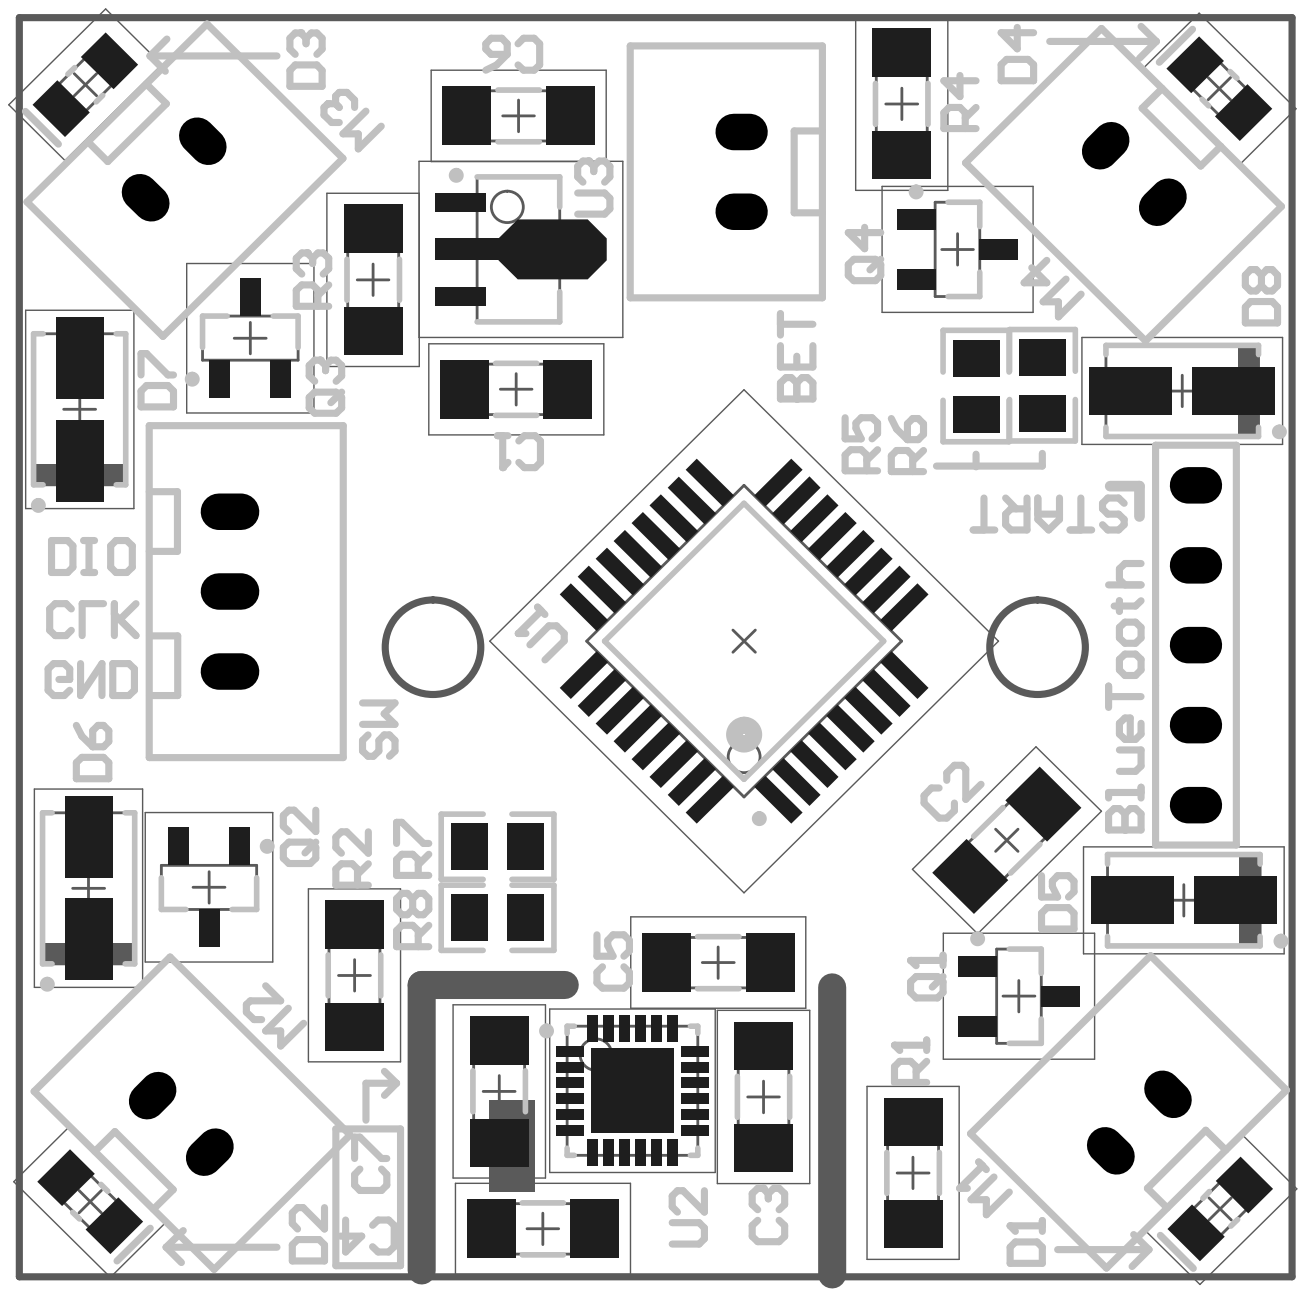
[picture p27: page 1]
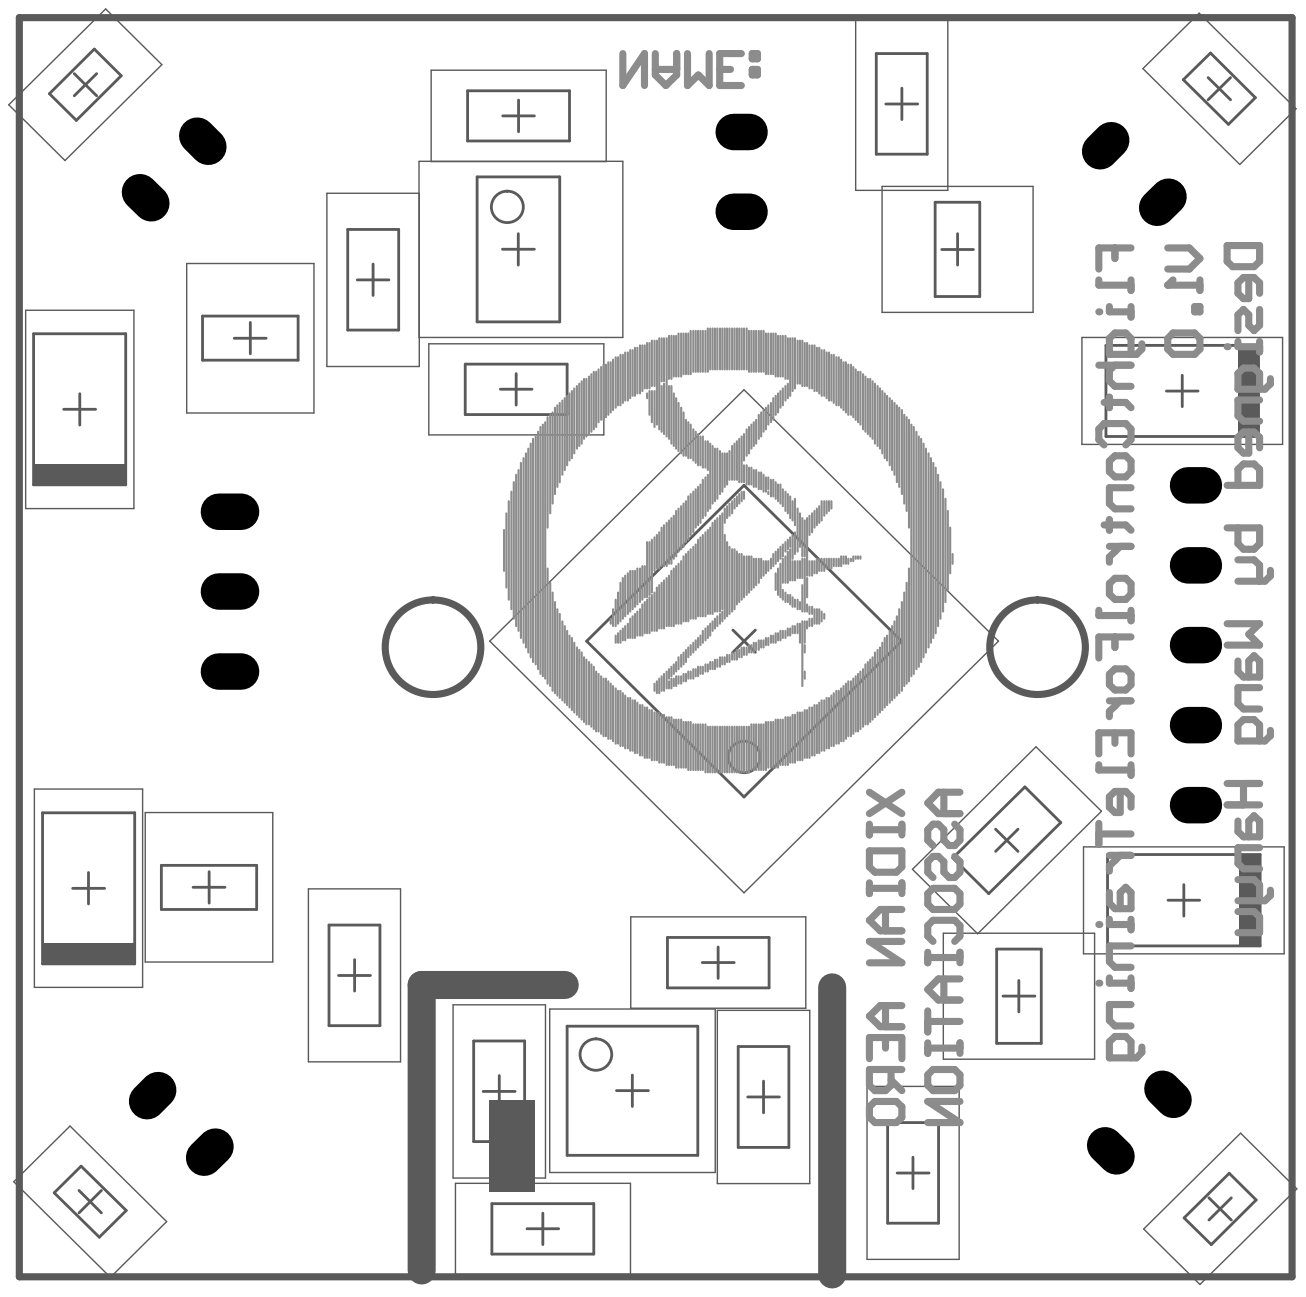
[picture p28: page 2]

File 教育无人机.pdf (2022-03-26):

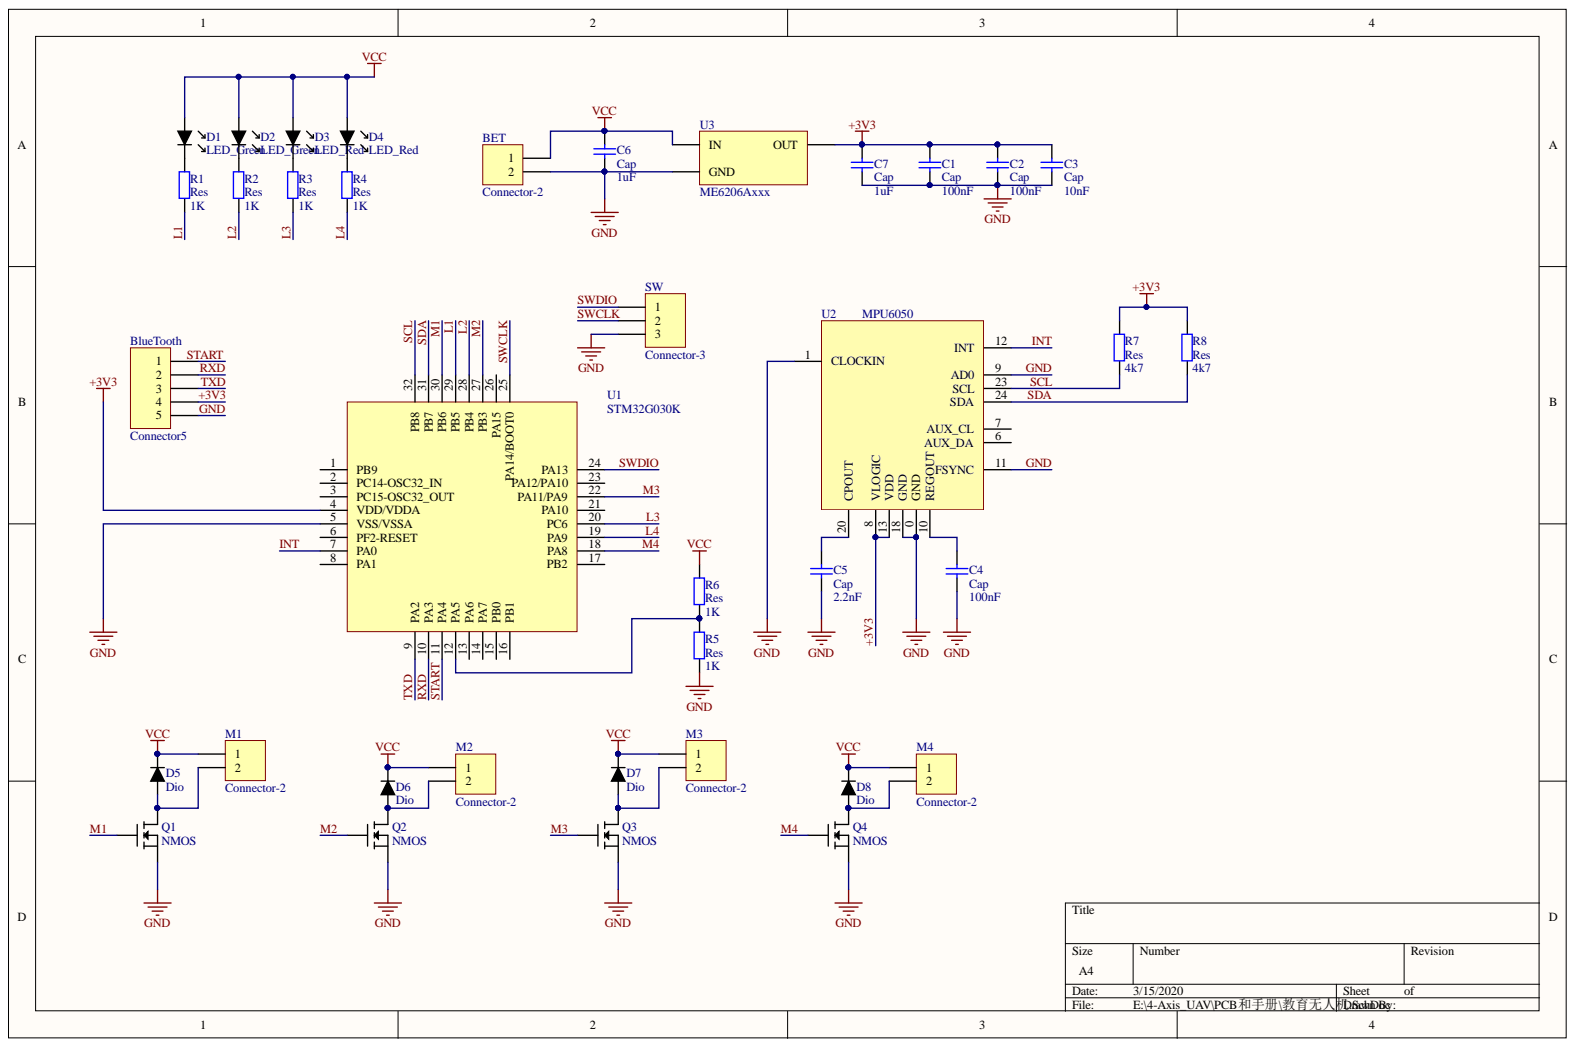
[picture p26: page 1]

PC14-OSC32_IN 2 | M3

VDD/VDDA 4 | L3
VSS/VSSA 5

INT | PF2-RESET 6 | L4

Size A4 | Number | Revision

Date: 3/15/2020 | Sheet of
File: E:\4-Axis_UAV\PCB和手册\教育无人机D.rSacwhDn Bocy:
